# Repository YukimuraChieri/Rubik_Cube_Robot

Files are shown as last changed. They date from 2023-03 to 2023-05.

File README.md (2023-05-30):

# Rubik_Cube_Robot
## 毕业设计：双臂二指魔方机器人  
该项目完成于2022年6月  
整体结构图如下：  
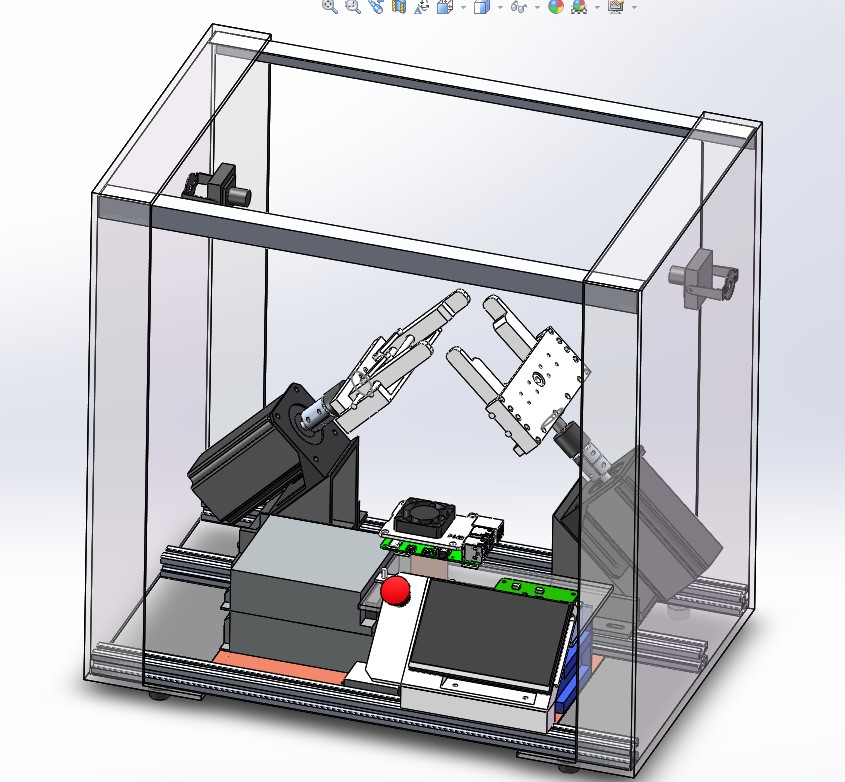
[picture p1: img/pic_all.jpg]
  
该机器人使用两个闭环步进电机驱动夹爪旋转，使用高速舵机驱动夹爪动作。  
机器人的控制系统主要为下位机+上位机，下位机与上位机之间通过USB串口通信  
下位机硬件基于STM32F103C8T6制作，上位机硬件为树莓派4B，操作系统为Ubuntu+ROS。  
其中上位机外接了一个触摸屏用于显示人机交互界面，该界面采用Qt开发。
仓库中的catkin_ws为ROS部分的代码。  
Robot_HMI为Qt界面的代码。  
matlab程序为计算S曲线加减速的相关代码。  

## 注意事项  
STM32下位机程序的开发环境为keil5，如果出现乱码的情况需要将编码设置为GB2312。  
PCB工程需要使用Altium Designer09软件打开。  
整体结构需要使用solidworks2015或者以上版本的软件打开。  
  
更多细节见《毕业论文_最终版1》

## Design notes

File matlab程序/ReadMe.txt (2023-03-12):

test_1.m 为步进电机S曲线加减速曲线绘制程序
test_2.m 步进电机S曲线加减速脉冲周期序列生成程序

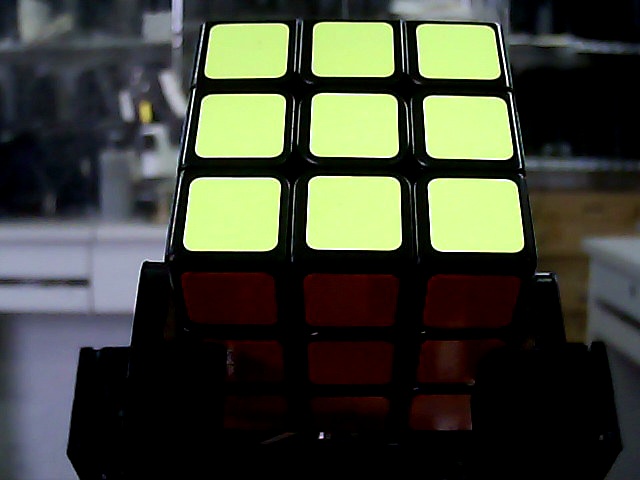
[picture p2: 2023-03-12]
catkin_ws/src/face_read/img/right_face12185.jpg

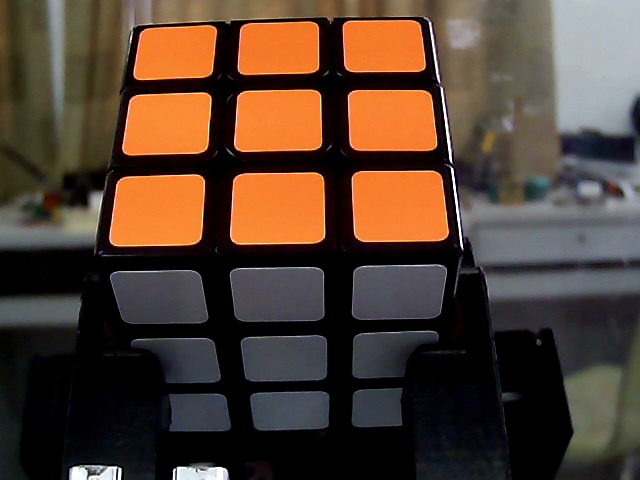
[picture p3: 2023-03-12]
catkin_ws/src/face_read/img/left_face12185.jpg

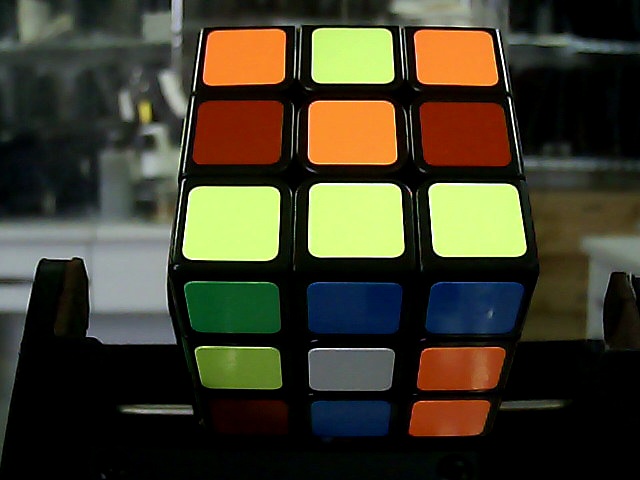
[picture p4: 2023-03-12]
catkin_ws/src/face_read/img/right_face7710.jpg

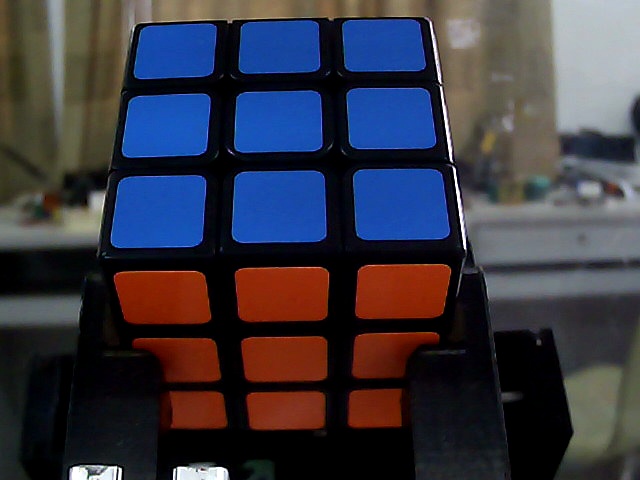
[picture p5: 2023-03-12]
catkin_ws/src/face_read/img/left_face12473.jpg

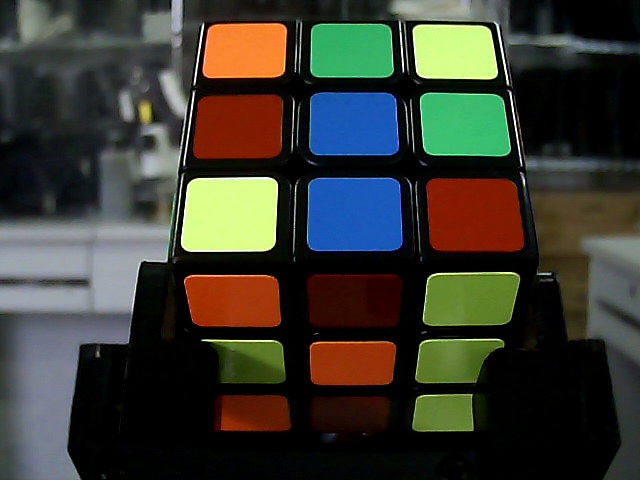
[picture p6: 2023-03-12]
catkin_ws/src/face_read/img/right_face8291.jpg

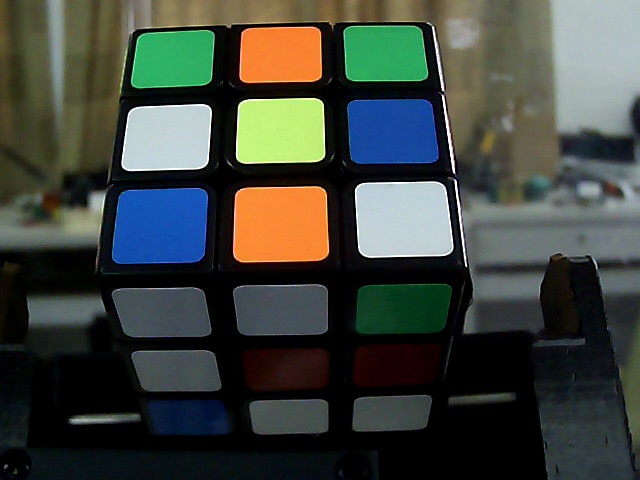
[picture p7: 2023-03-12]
catkin_ws/src/face_read/img/left_face7710.jpg

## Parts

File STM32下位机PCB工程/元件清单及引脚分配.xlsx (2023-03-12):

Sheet: Sheet1
STM32控制板元件清单
序号 | 名称 | 封装 | 数量 | 单价 | 备注
1 | STM32F103C8T6 | LQF-48 | 1 | 5 | MCU
2 | TLP521-1 | SOP-4 | 2 | 0.35 | 光耦隔离器件
3 | AMS1117-3.3 | SOT-223 | 1 |  | 3.3V LDO稳压芯片
4 | S8550 | SOT-23R | 6 |  | PNP三极管
5 | 8M贴片晶振 | SMD-5032 | 1
6 | A型6.3V10uf 106E钽电容 | 0805 | 2 | 0.41
7 | 104贴片电容 | 0805 | 9 | 0.02
8 | 20pF贴片电容 | 0805 | 2
9 | 贴片LED | 0805 | 2
10 | 22R贴片电阻 | 0805 | 2
11 | 330R贴片电阻 | 0805 | 2
12 | 1K贴片电阻 | 0805 | 6
13 | 4.7K贴片电阻 | 0805 | 6
14 | 10K贴片电阻 | 0805 | 3
15 | mini usb母座 | USB/SM0.8-6H5 | 1 | 0.11 | Mini USB接口
16 | 3P接线端子 | KF301-3P | 2 |  | 电机接口
17 | 4P接线端子 | KF301-4P | 1 |  | 电源接口
18 | 3P直排针 | HDR1X3 | 2 |  | 舵机接口
19 | 4P直排针 | HDR1X4 | 2 |  | SWD、串口接口
20 | XH2.54MM插座 | HDR1X2 | 1 |  | 紧急开关接口
21 | PCB |  | 1 |  | 需要在PCB生产厂家打样

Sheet: Sheet2
STM32控制板元件清单
序号 | 名称 | 封装 | 数量 | 备注
1 | STM32F103C8T6 | LQF-48 | 1 | MCU
2 | TLP521-1 | SOP-4 | 2 | 光耦隔离器件
3 | AMS1117-3.3 | SOT-223 | 1 | 3.3V LDO稳压芯片
4 | S8550 | SOT-23R | 6 | PNP三极管
5 | 8M贴片晶振 | SMD-5032 | 1
6 | A型6.3V10uf 106E钽电容 | 0805 | 2
7 | 104贴片电容 | 0805 | 9
8 | 20pF贴片电容 | 0805 | 2
9 | 贴片LED | 0805 | 2
10 | 22R贴片电阻 | 0805 | 2
11 | 330R贴片电阻 | 0805 | 2
12 | 1K贴片电阻 | 0805 | 6
13 | 4.7K贴片电阻 | 0805 | 6
14 | 10K贴片电阻 | 0805 | 3
15 | mini usb母座 | USB/SM0.8-6H5 | 1 | Mini USB接口
16 | 3P接线端子 | KF301-3P | 2 | 电机接口
17 | 4P接线端子 | KF301-4P | 1 | 电源接口
18 | 3P直排针 | HDR1X3 | 2 | 舵机接口
19 | 4P直排针 | HDR1X4 | 2 | SWD、串口接口
20 | XH2.54MM插座 | HDR1X2 | 1 | 紧急开关接口

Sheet: IO分配表
IO端口分配表
引脚 | 功能 |  | 备注
PB13 | PUL1 | 电机1 | TIM1_CH1N
PA4 | DIR1
PA5 | ENA1
PB14 | PUL2 | 电机2 | TIM1_CH2N
PA7 | DIR2
PB0 | ENA2
PB6 | PWM1 | 舵机1 | TIM4_CH1
PB7 | PWM2 | 舵机2 | TIM4_CH2
PA9 | TXD1 | 串口1
PA10 | RXD1
PA11 | D- | USB接口
PA12 | D+
PA13 | SWDIO | SWD接口
PA14 | SWCLK
PB12 |  | 紧急开关 | TIM1_BKIN
PC13 | LED1 | LED指示灯

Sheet: 通信协议格式
通信协议格式
执行指令 | AT
应答 | OK
参数说明
舵机操作指令
执行指令 | AT+SERVO=<LR>,<CMD>
应答 | AT+SERVO OK
参数说明 | <LR> | LEFT:左舵机 | RIGHT:右舵机 | ALL:所有舵机
 | <CMD> | CLAMP:夹紧 | LOOSE:松开
步进电机操作指令
执行指令 | AT+STEP=<LR>,<DIR>,<ANG>
应答 | AT+STEP OK
参数说明 | <LR> | LEFT:左电机 | RIGHT:右电机 | ALL:所有电机
 | <DIR> | ‘+’：顺时针旋转 | ‘-’：逆时针旋转
 | <ANG> | 90：90度 | 180：180度
应答 | Error
说明 | 指令格式错误
应答 | Alarm
说明 | 急停开关按下
 |  | AT+SERVO=RIGHT,LOOSE
 |  | AT+STEP=RIGHT,+,180

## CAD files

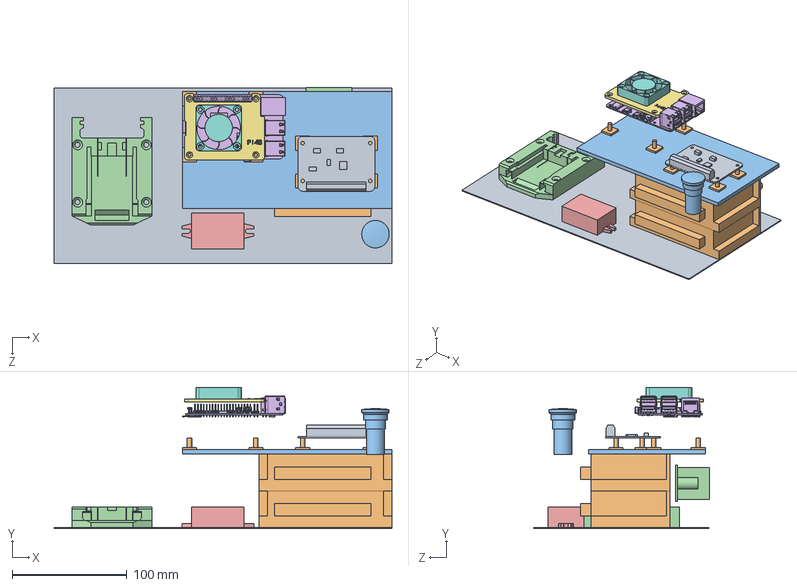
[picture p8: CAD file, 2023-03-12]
魔方机器人整体结构/电控部分/装配体_电池.SLDASM
295.0 x 123.3 x 153.5 mm
底板
电机驱动器 x 2
亚克力板
DC12V转7.5V稳压模块
DC12V转5V稳压模块
Raspberry Pi 41
风扇支架
风扇4010
STM32控制板
塑料座 x 8
急停开关
电池卡座_V3

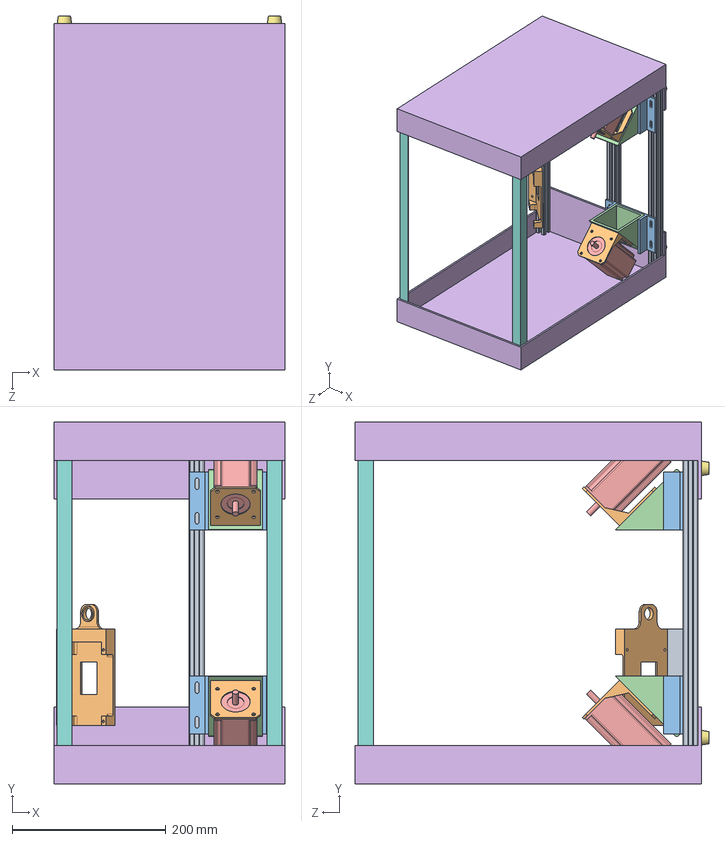
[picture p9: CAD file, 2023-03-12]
魔方机器人整体结构/底座/底座_装配体.SLDASM
300.0 x 470.0 x 460.0 mm
2020铝型材_350 x 3
电机支架 x 2
电机座1 x 2
电机座2 x 2
57步进电机 x 2
亚克力支架 x 2
脚垫20-17-10 x 4
L铝型材_460 x 2
触摸屏底座
屏幕支架

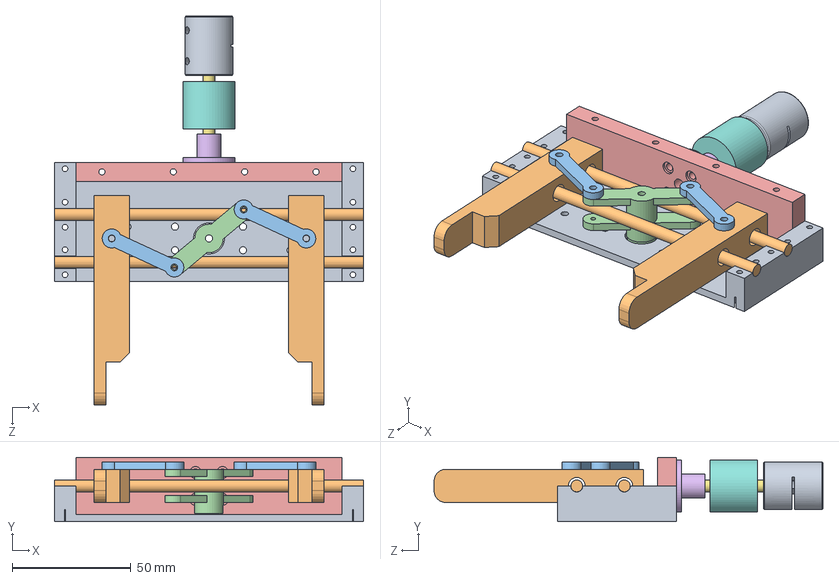
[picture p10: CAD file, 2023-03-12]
魔方机器人整体结构/魔方平行夹/装配体1.SLDASM
130.0 x 27.0 x 163.5 mm
底座
滑轴 x 2
连杆2 x 2
主轴连杆
后卡位片_更改
法兰联轴器
M5光轴_50
导电滑环
联轴器
滑块2 x 2

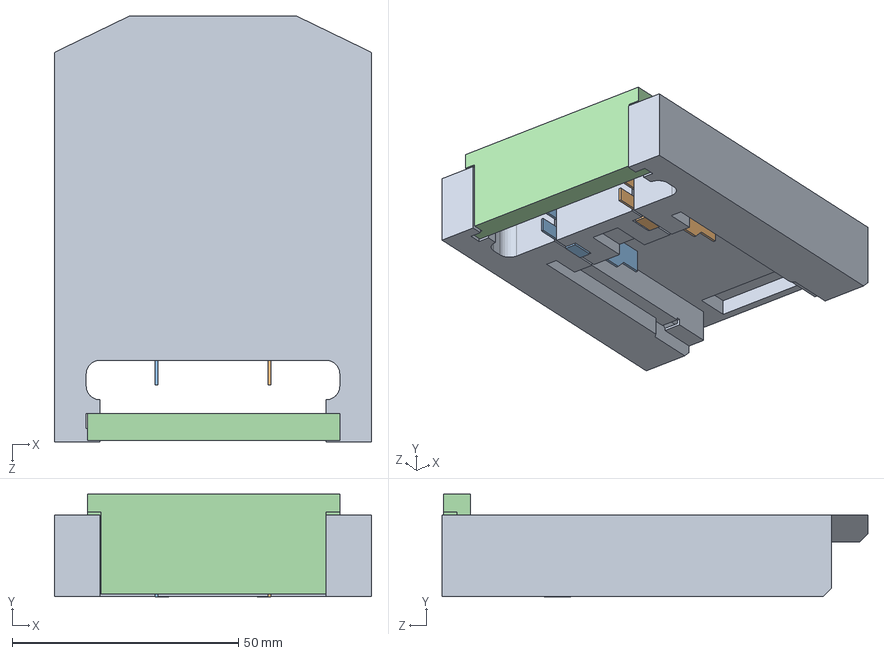
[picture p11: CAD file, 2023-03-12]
魔方机器人整体结构/电池卡座/电池座.SLDASM
70.0 x 22.7 x 94.0 mm
电池卡座
电极片左
电极片右
盖板

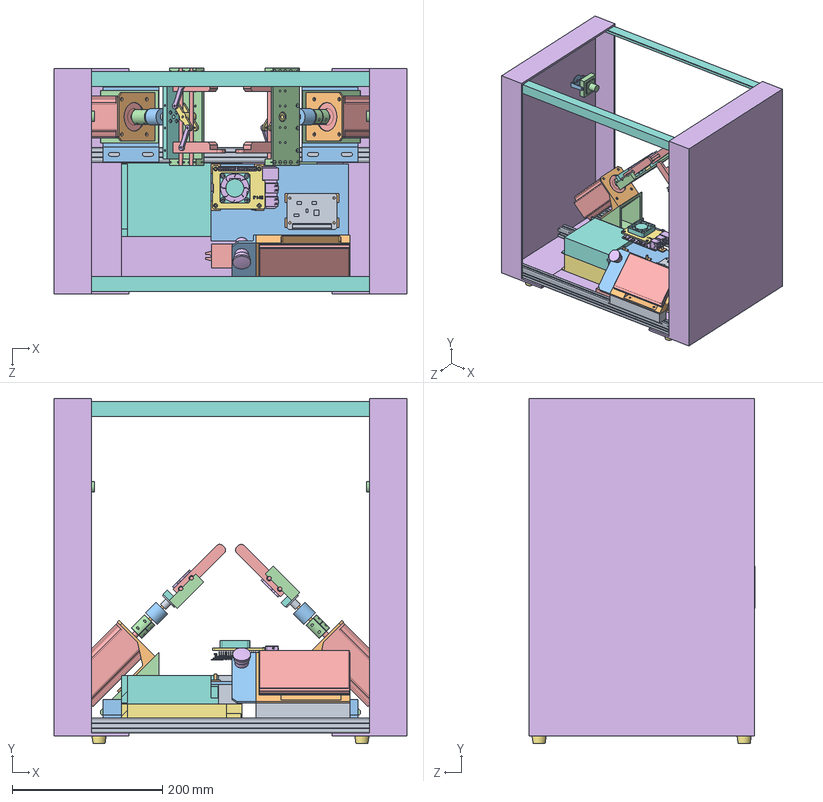
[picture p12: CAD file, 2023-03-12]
魔方机器人整体结构/总装配体.SLDASM
470.0 x 460.0 x 300.9 mm
2020铝型材_350 x 3
电机支架 x 2
电机座1 x 2
电机座2 x 2
57步进电机 x 2
亚克力支架 x 2
脚垫20-17-10 x 4
L铝型材_460 x 2
触摸屏底座
屏幕支架
屏幕侧板
底座 x 2
滑轴 x 4
连杆2 x 4
主轴连杆 x 2
后卡位片_更改 x 2
法兰联轴器 x 2
M5光轴_50 x 2
导电滑环 x 2
联轴器 x 2
滑块2 x 4
底板
12V开关电源
28V开关电源
侧板
电机驱动器 x 2
亚克力板
DC12V转7.5V稳压模块
DC12V转5V稳压模块
Raspberry Pi 41
风扇支架
风扇4010
STM32控制板
塑料座 x 8
摄像头支架 x 2
摄像头 x 2
触摸屏
急停开关

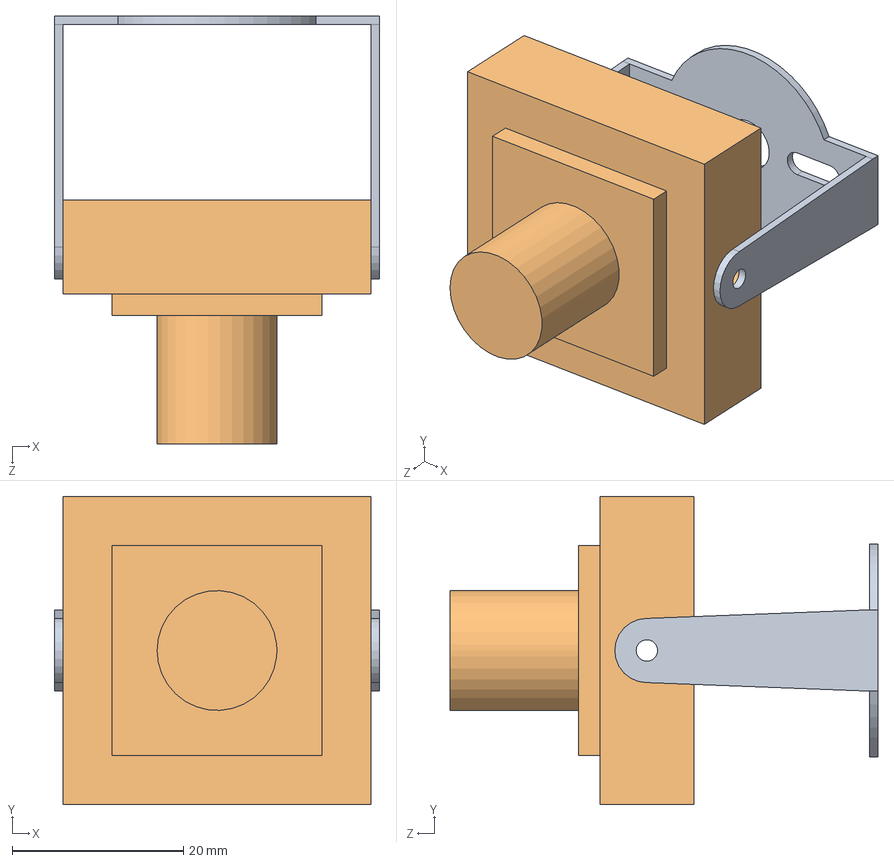
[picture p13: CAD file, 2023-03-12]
魔方机器人整体结构/电控部分/USB摄像头.SLDASM
38.0 x 36.0 x 50.0 mm
摄像头支架
摄像头

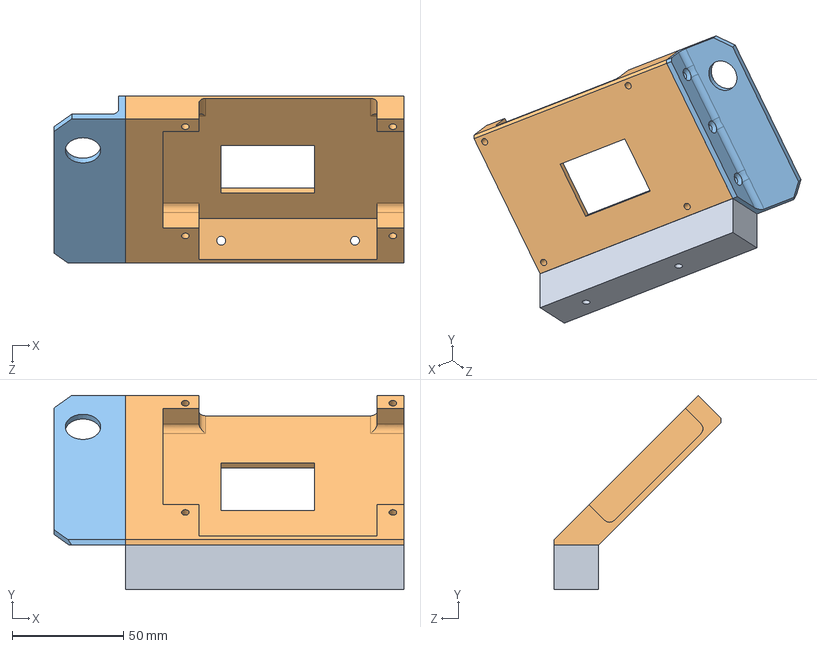
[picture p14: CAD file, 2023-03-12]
魔方机器人整体结构/底座/触摸屏支架.SLDASM
157.0 x 87.2 x 75.0 mm
触摸屏底座
屏幕支架
屏幕侧板

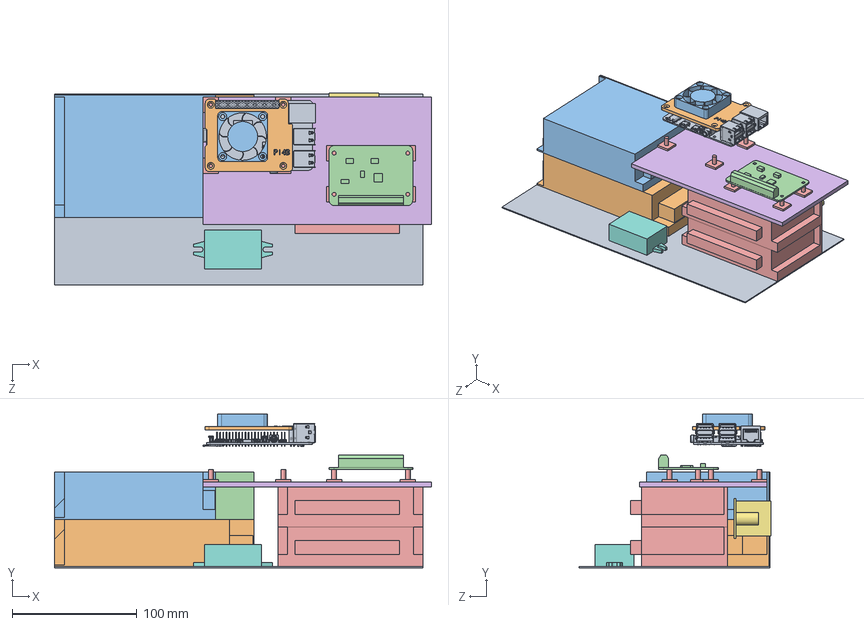
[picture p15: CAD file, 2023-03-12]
魔方机器人整体结构/电控部分/装配体2.SLDASM
302.0 x 123.3 x 153.5 mm
底板
12V开关电源
28V开关电源
侧板
电机驱动器 x 2
亚克力板
DC12V转7.5V稳压模块
DC12V转5V稳压模块
Raspberry Pi 41
风扇支架
风扇4010
STM32控制板
塑料座 x 8

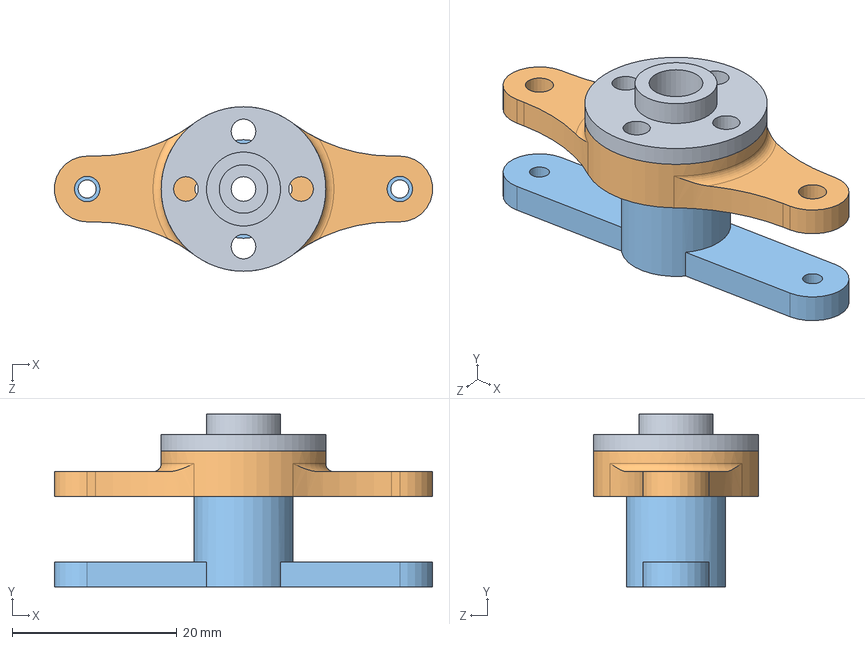
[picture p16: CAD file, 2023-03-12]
魔方机器人整体结构/魔方平行夹/主轴连杆_装配体.SLDASM
45.9 x 21.0 x 20.0 mm
舵机舵盘
主轴连杆下_2022_4_21
主轴连杆上2

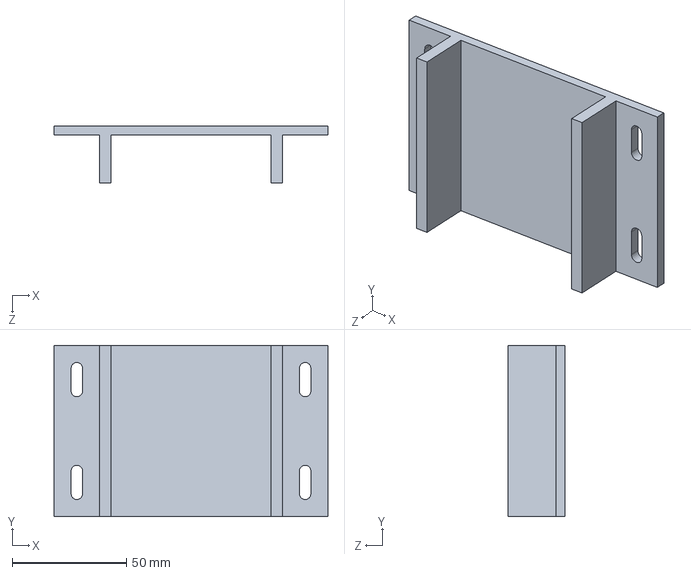
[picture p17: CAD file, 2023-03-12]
魔方机器人整体结构/底座/电机座1.SLDPRT
120.0 x 75.0 x 25.0 mm

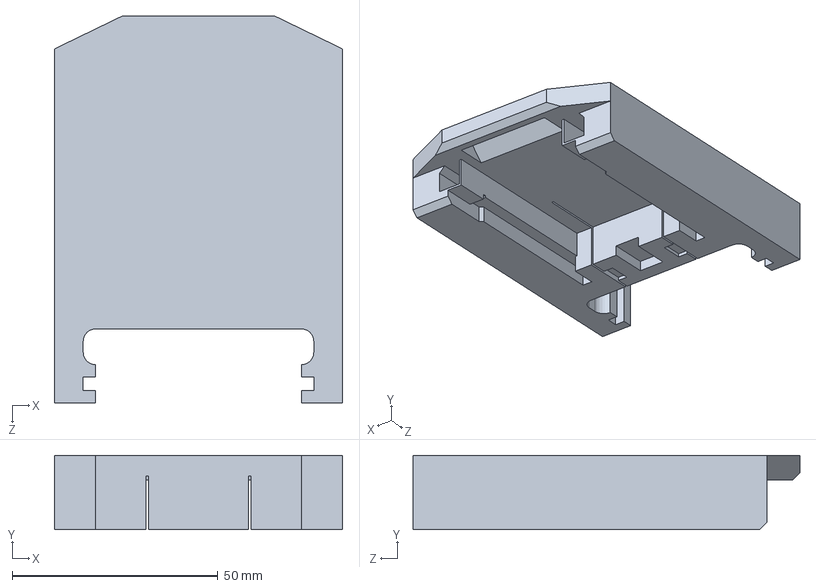
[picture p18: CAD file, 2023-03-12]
魔方机器人整体结构/电池卡座/电池卡座.SLDPRT
70.0 x 18.0 x 94.0 mm

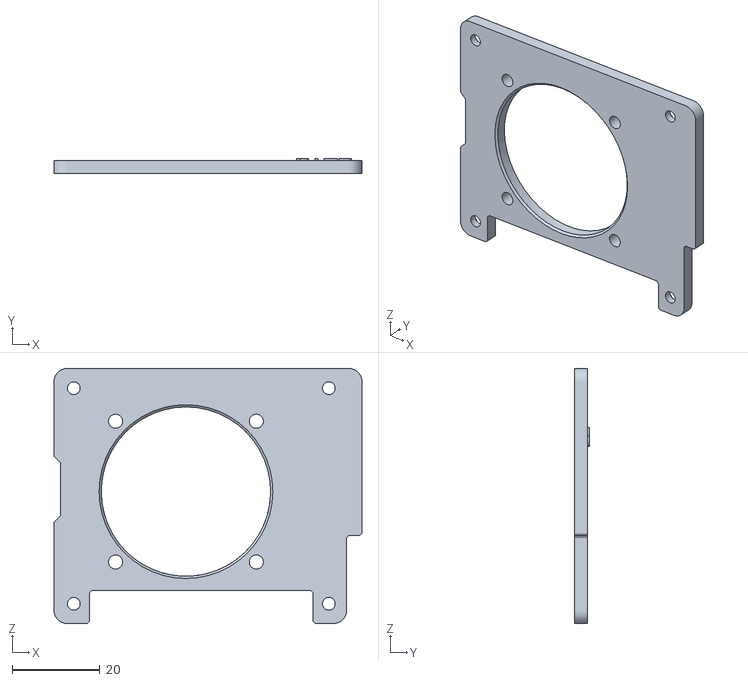
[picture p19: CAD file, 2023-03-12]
魔方机器人整体结构/风扇支架.STL
70.0 x 3.45 x 58.0

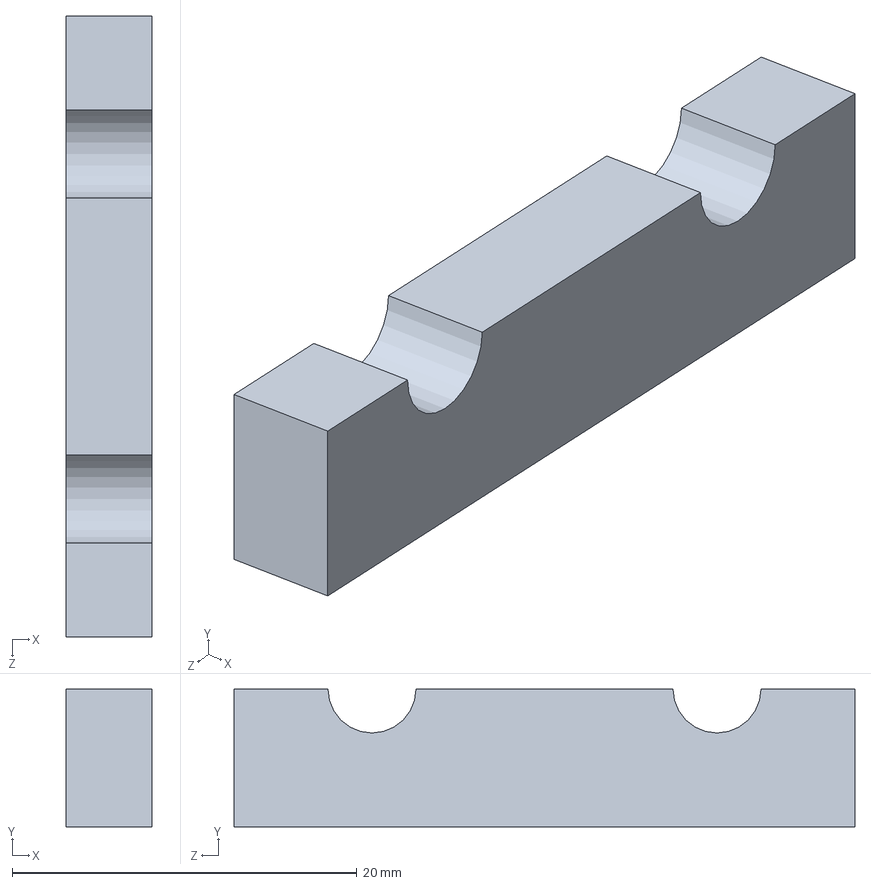
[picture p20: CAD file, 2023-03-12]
魔方机器人整体结构/魔方平行夹/夹块.SLDPRT
5.00 x 8.00 x 36.0 mm

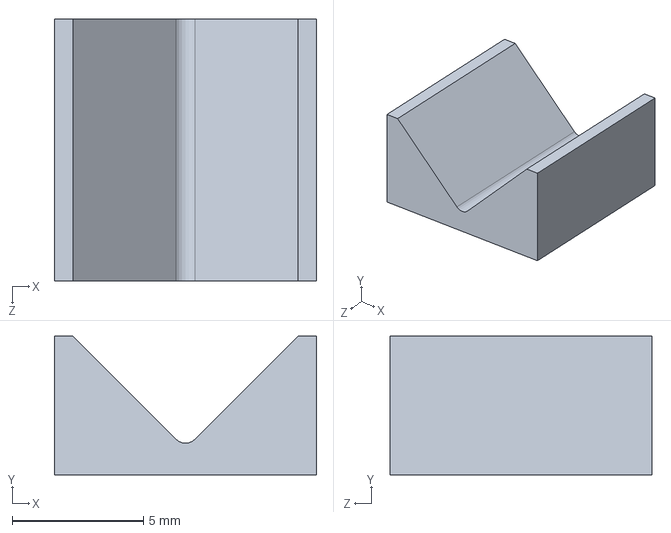
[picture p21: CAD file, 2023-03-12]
魔方机器人整体结构/灯条固定座1.SLDPRT
10.0 x 5.29 x 10.0 mm

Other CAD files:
魔方机器人整体结构/电控部分/塑料座.SLDPRT
魔方机器人整体结构/电池卡座/电极片.SLDPRT
魔方机器人整体结构/魔方平行夹/主轴连杆下2.SLDPRT
魔方机器人整体结构/屏幕侧板.STL
魔方机器人整体结构/主轴连杆下.SLDPRT
魔方机器人整体结构/主轴连杆下.STL
魔方机器人整体结构/主轴连杆下_2022_5_2.STL
魔方机器人整体结构/屏幕支架.STL
魔方机器人整体结构/底座/2020铝型材.SLDPRT
魔方机器人整体结构/底座/2020铝型材_150.SLDPRT
魔方机器人整体结构/底座/2020铝型材_350.SLDPRT
魔方机器人整体结构/底座/2020铝型材_80.SLDPRT
魔方机器人整体结构/底座/57步进电机.SLDPRT
魔方机器人整体结构/底座/L铝型材_460.SLDPRT
魔方机器人整体结构/底座/M5光轴_50.SLDPRT
魔方机器人整体结构/底座/亚克力支架.SLDPRT
魔方机器人整体结构/底座/亚克力板_加工.DWG
魔方机器人整体结构/底座/亚克力板_加工.SLDDRW
魔方机器人整体结构/底座/亚克力板_加工.SLDPRT
魔方机器人整体结构/底座/导电滑环.SLDPRT
魔方机器人整体结构/底座/屏幕侧板.SLDPRT
魔方机器人整体结构/底座/屏幕支架.SLDPRT
魔方机器人整体结构/底座/底板.SLDPRT
魔方机器人整体结构/底座/电机座2.SLDPRT
魔方机器人整体结构/底座/电机支架.SLDPRT
魔方机器人整体结构/底座/联轴器.SLDPRT
魔方机器人整体结构/底座/脚垫20-17-10.sldprt
魔方机器人整体结构/底座/触摸屏底座.SLDPRT
魔方机器人整体结构/滑环垫片.SLDPRT
魔方机器人整体结构/灯条固定座1.STL
魔方机器人整体结构/灯条封头.SLDPRT
魔方机器人整体结构/灯条封头.STL
魔方机器人整体结构/电控部分/12V开关电源.SLDPRT
魔方机器人整体结构/电控部分/28V开关电源.SLDPRT
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

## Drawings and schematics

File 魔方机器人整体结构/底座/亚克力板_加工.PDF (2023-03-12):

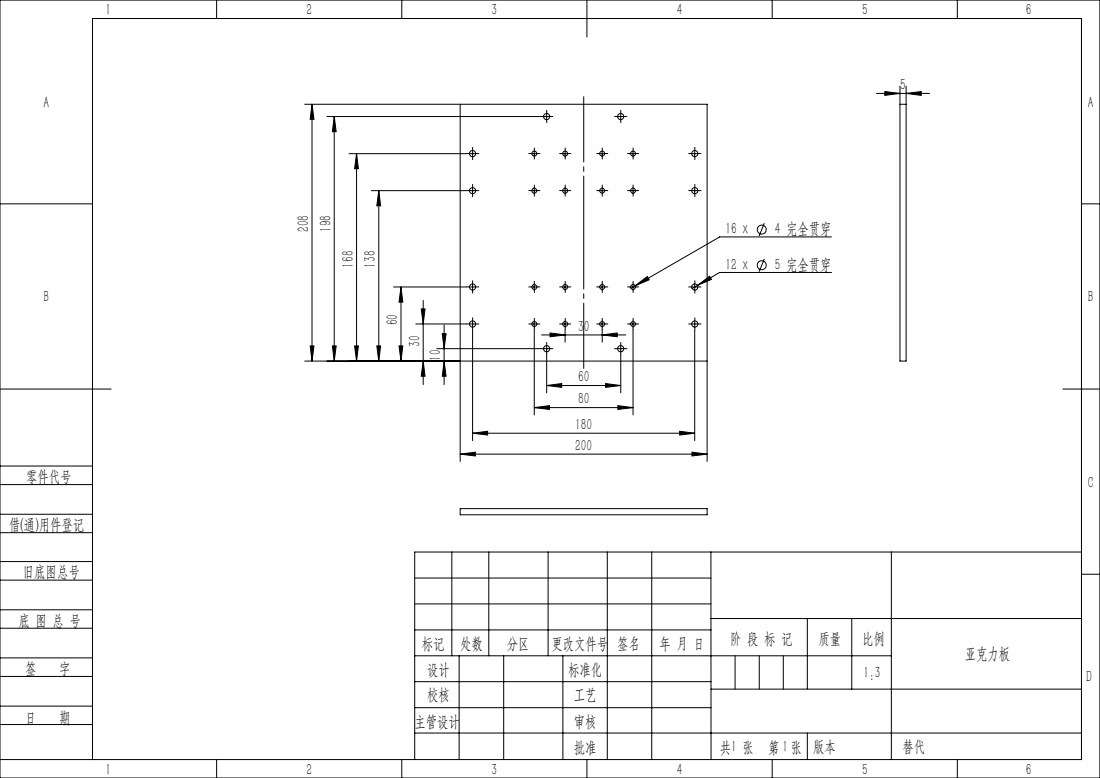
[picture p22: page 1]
5 完全贯穿; 4 完全贯穿

阶 段 标 记 | 质量 | 比例 | 亚克力板

标记 | 处数 | 分区 | 更改文件号 | 签名 | 年 月 日

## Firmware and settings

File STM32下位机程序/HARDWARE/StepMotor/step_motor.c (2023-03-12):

#include "step_motor.h"

// 旋转列表指针
u16* S_Curve_List;
u16 len;						// 长度
u8 motor_AB = '\0';	// 左右电机选择
u8 stepRun = 0;			// 电机运行状态
u8 brkFlag = 0;			// 刹车信号
u16 PulCnt = 0;			// 脉冲计数
u8 stepFinish = 0;	// 电机完成状态


// S曲线低速旋转90度脉冲周期列表，最大加速度20r/s^2，加减速时间0.1S
const u16 Rot90_LS_List[250] = {
	9999,	9523,	8398,	7194,	6185,	5396,	4783,	4300,	3911,	3594,	
	3329,	3105,	2914,	2747,	2602,	2473,	2359,	2256,	2164,	2080,	
	2003,	1933,	1868,	1809,	1754,	1702,	1655,	1611,	1571,	1535,	
	1502,	1471,	1442,	1416,	1391,	1368,	1347,	1327,	1308,	1290,	
	1273,	1257,	1241,	1227,	1213,	1200,	1188,	1176,	1164,	1154,	
	1143,	1133,	1124,	1115,	1106,	1098,	1090,	1082,	1075,	1067,	
	1061,	1054,	1048,	1041,	1035,	1030,	1024,	1019,	1014,	1009,	
	1004,	1000,	995,	991,	987,	983,	979,	975,	972,	968,	
	965,	962,	959,	956,	953,	950,	948,	945,	943,	940,	
	938,	936,	934,	932,	930,	928,	926,	925,	923,	922,	
	920,	919,	918,	917,	916,	915,	914,	913,	912,	911,	
	911,	910,	910,	909,	909,	909,	908,	908,	908,
	908,	908,	908,	908,	908,	908,	908,	908,	908,	908,	
	908,	908,	908,	908,	909,	909,	909,	910,	910,	911,	
	911,	912,	913,	914,	915,	916,	917,	918,	919,	920,	
	922,	923,	925,	926,	928,	930,	932,	934,	936,	938,	
	940,	943,	945,	948,	950,	953,	956,	959,	962,	965,	
	968,	972,	975,	979,	983,	987,	991,	995,	1000,	1004,	
	1009,	1014,	1019,	1024,	1030,	1035,	1041,	1048,	1054,	1061,	
	1067,	1075,	1082,	1090,	1098,	1106,	1115,	1124,	1133,	1143,	
	1154,	1164,	1176,	1188,	1200,	1213,	1227,	1241,	1257,	1273,	
	1290,	1308,	1327,	1347,	1368,	1391,	1416,	1442,	1471,	1502,	
	1535,	1571,	1611,	1655,	1702,	1754,	1809,	1868,	1933,	2003,	
	2080,	2164,	2256,	2359,	2473,	2602,	2747,	2914,	3105,	3329,	
	3594,	3911,	4300,	4783,	5396,	6185,	7194,	8398,	9523,	9999, 1
};

// S曲线低速旋转180度脉冲周期列表，最大加速度20r/s^2，加减速时间0.2S
const u16 Rot180_LS_List[501] = {
	9999,	9090,	7328,	5888,	4892,	4194,	3684,	3297,	2993,	2747,	
	2544,	2374,	2228,	2102,	1993,	1896,	1809,	1732,	1662,	1599,	
	1541,	1488,	1439,	1394,	1352,	1313,	1277,	1243,	1212,	1182,	
	1154,	1127,	1102,	1078,	1056,	1035,	1014,	995,	976,	959,	
	942,	925,	910,	895,	881,	868,	855,	843,	832,	821,	
	811,	801,	792,	783,	774,	766,	758,	750,	743,	736,	
	729,	723,	716,	710,	704,	699,	693,	688,	682,	677,	
	672,	668,	663,	659,	654,	650,	646,	642,	638,	634,	
	631,	627,	624,	620,	617,	614,	610,	607,	604,	601,	
	599,	596,	593,	590,	588,	585,	583,	580,	578,	575,	
	573,	571,	569,	567,	564,	562,	560,	558,	556,	555,	
	553,	551,	549,	547,	546,	544,	542,	541,	539,	537,	
	536,	534,	533,	532,	530,	529,	527,	526,	525,	523,	
	522,	521,	520,	519,	517,	516,	515,	514,	513,	512,	
	511,	510,	509,	508,	507,	506,	505,	504,	503,	502,	
	502,	501,	500,	499,	498,	498,	497,	496,	495,	495,	
	494,	493,	493,	492,	491,	491,	490,	489,	489,	488,	
	488,	487,	487,	486,	486,	485,	485,	484,	484,	483,	
	483,	483,	482,	482,	481,	481,	481,	480,	480,	480,	
	479,	479,	479,	479,	478,	478,	478,	478,	477,	477,	
	477,	477,	477,	476,	476,	476,	476,	476,	476,	476,	
	476,	475,	475,	475,	475,	475,	475,	475,	475,	475,	
	475,	475,	475,	475,	475,	475,	475,	475,	475,	475,	
	475,	475,	475,	475,	475,	475,	475,	475,	475,	475,	
	475,	475,	475,	475,	475,	475,	475,	475,	475,	475,	
	475,	475,	475,	475,	475,	475,	475,	475,	475,	475,	
	475,	475,	475,	475,	475,	475,	475,	475,	475,	475,	
	475,	475,	475,	475,	475,	475,	475,	475,	475,	475,	
	475,	475,	475,	475,	475,	475,	475,	475,	475,	476,	
	476,	476,	476,	476,	476,	476,	476,	477,	477,	477,	
	477,	477,	478,	478,	478,	478,	479,	479,	479,	479,	
	480,	480,	480,	481,	481,	481,	482,	482,	483,	483,	
	483,	484,	484,	485,	485,	486,	486,	487,	487,	488,	
	488,	489,	489,	490,	491,	491,	492,	493,	493,	494,	
	495,	495,	496,	497,	498,	498,	499,	500,	501,	502,	
	502,	503,	504,	505,	506,	507,	508,	509,	510,	511,	
	512,	513,	514,	515,	516,	517,	519,	520,	521,	522,	
	523,	525,	526,	527,	529,	530,	532,	533,	534,	536,	
	537,	539,	541,	542,	544,	546,	547,	549,	551,	553,	
	555,	556,	558,	560,	562,	564,	567,	569,	571,	573,	
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
};


// S曲线中速旋转90度脉冲周期列表，最大加速度40r/s^2，加减速时间0.1S
const u16 Rot90_MS_List[250] = {
	9999,	7142,	4596,	3459,	2824,	2414,	2124,	1907,	1737,	1600,	
	1487,	1392,	1311,	1240,	1178,	1123,	1074,	1030,	991,	954,	
	921,	891,	864,	840,	818,	798,	780,	763,	748,	733,	
	720,	708,	696,	685,	675,	666,	657,	648,	640,	633,	
	626,	619,	612,	606,	600,	594,	589,	584,	579,	574,	
	570,	565,	561,	557,	554,	550,	546,	543,	540,	537,	
	534,	531,	528,	525,	523,	520,	518,	516,	513,	511,	
	509,	507,	505,	504,	502,	500,	499,	497,	496,	494,	
	493,	492,	490,	489,	488,	487,	486,	485,	484,	483,	
	482,	482,	481,	480,	480,	479,	478,	478,	477,	477,	
	477,	476,	476,	476,	476,	475,	475,	475,	475,	
	475,	475,	475,	475,	475,	475,	475,	475,	475,	475,		
	475,	475,	475,	475,	475,	475,	475,	475,	475,	475,	
	475,	475,	475,	475,	475,	475,	475,	475,	475,	475,	
	475,	475,	475,	475,	475,	476,	476,	476,	476,	477,	
	477,	477,	478,	478,	479,	480,	480,	481,	482,	482,	
	483,	484,	485,	486,	487,	488,	489,	490,	492,	493,	
	494,	496,	497,	499,	500,	502,	504,	505,	507,	509,	
	511,	513,	516,	518,	520,	523,	525,	528,	531,	534,	
	537,	540,	543,	546,	550,	554,	557,	561,	565,	570,	
	574,	579,	584,	589,	594,	600,	606,	612,	619,	626,	
	633,	640,	648,	657,	666,	675,	685,	696,	708,	720,	
	733,	748,	763,	780,	798,	818,	840,	864,	891,	921,	
	954,	991,	1030,	1074,	1123,	1178,	1240,	1311,	1392,	1487,	
	1600,	1737,	1907,	2124,	2414,	2824,	3459,	4596,	7142,	9999,	 1
};
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

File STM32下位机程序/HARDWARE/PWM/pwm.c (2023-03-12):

#include "pwm.h"

u8 servoRun = 0;		// 舵机运行状态
u8 leftAngle = 0;		// 左舵机当前角度
u8 rightAngle = 0;	// 右舵机当前角度
u8 setLeft = 0;			// 左舵机设定角度
u8 setRight = 0;		// 右舵机设定角度
u8 servoFinish = 0;	// 舵机完成状态
u8 servo_speed = 4;	// 舵机夹紧速度

void TIM4_PWM_Init(u16 arr,u16 psc)
{
	//此部分需手动修改IO口设置
	RCC->APB1ENR|=1<<2; 		//TIM4时钟使能    
	RCC->APB2ENR|=1<<3;    	//使能PORTB时钟 	 
	GPIOB->CRL&=0X00FFFFFF;	//PB6/7输出
	GPIOB->CRL|=0XBB000000;	//复用功能输出

	TIM4->ARR=arr;			//设定计数器自动重装值 
	TIM4->PSC=psc;			//预分频器分频数
//	TIM4->DIER|=1<<0;		//允许更新中断
	
	TIM4->CCMR1|=7<<4;  	//CH1 PWM2模式		 
	TIM4->CCMR1|=1<<3; 		//CH1 预装载使能
	TIM4->CCER|=1<<1;   	//OC1 输出反相
	TIM4->CCER|=1<<0;			//OC1 输出使能	 

	TIM4->CCMR1|=7<<12;		//CH2 PWM2模式		 
	TIM4->CCMR1|=1<<11;		//CH2 预装载使能	   
	TIM4->CCER|=1<<5;   	//OC2 输出反相
	TIM4->CCER|=1<<4;			//OC2 输出使能
	
	TIM4->CR1=0x0080;   //ARPE使能 
	TIM4->CR1|=0x01;    //使能定时器4
	
	CH1_PWM_VAL = Angle_to_PWM(0);	//初始化右舵机PWM占空比
	CH2_PWM_VAL = Angle_to_PWM(0);	//初始化左舵机PWM占空比
	
	MY_NVIC_Init(1,2,TIM4_IRQn,2);		//抢占1，子优先级2，组2
}

//角度值转换为PWM比较值（适用于180度舵机 ）
u16 Angle_to_PWM(u16 angle)
{
	angle = angle * 4 + 180;
	
	return 7200 - angle;
}


//设置舵机角度函数
void Set_Angle(u8 angle, char dir)
{
	switch(dir)
	{
		case 'A':	setLeft = angle;	break;
		case 'B':	setRight = angle;	break;
	}
	
	if(setLeft != leftAngle || setRight != rightAngle)
	{
		TIM4->DIER |= 1<<0;	// 允许更新中断
		servoRun = 1;				// 舵机运行状态置1
	}
	else
		servoFinish = 1;				// 舵机完成状态置1
}


// 获取舵机的运行状态
u8 Get_Servo_Status(void)
{
	return servoRun;		// 返回舵机运行状态
}


// 获取舵机的完成状态
u8 Get_Servo_Finish(void)
{
	u8 temp = servoFinish;
	
	servoFinish = 0;
	
	return temp;		// 返回舵机完成状态
}


// 设置舵机速度
void Set_Servo_Speed(u8 speed)
{
	servo_speed = speed;
}


// 定时器4中断服务函数
void TIM4_IRQHandler(void)
{
	if(TIM4->SR&0X0001)	//溢出中断
	{
		if(leftAngle < setLeft)	// 左舵机小于设定角度
		{
			leftAngle += (setLeft - leftAngle)/servo_speed + 1;
			CH2_PWM_VAL = Angle_to_PWM(leftAngle);
		}
		else if(leftAngle > setLeft)	// 左舵机大于设定角度
		{
			leftAngle -= (leftAngle - setLeft)/servo_speed + 1;
			CH2_PWM_VAL = Angle_to_PWM(leftAngle);
		}
		
		if(rightAngle < setRight)	// 右舵机小于设定角度
		{
			rightAngle += (setRight - rightAngle)/servo_speed + 1;
			CH1_PWM_VAL = Angle_to_PWM(rightAngle);
		}
		else if(rightAngle > setRight)	// 右舵机大于设定角度
		{
			rightAngle -= (rightAngle - setRight)/servo_speed + 1;
			CH1_PWM_VAL = Angle_to_PWM(rightAngle);
		}
		
		if(leftAngle == setLeft && rightAngle == setRight)	// 如果左右舵机均达到设定角度
		{
			servoRun = 0;						// 舵机运行状态置0
			servoFinish = 1;				// 舵机完成状态置1
			TIM4->DIER &= ~(1<<0);	// 关闭中断
		}
		
		TIM4->SR&=~(1<<0);	//清除中断标志位
	}
}

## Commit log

2023-03-12 项目提交
    [12V开关电源.SLDPRT, 2020铝型材.SLDPRT, 2020铝型材_150.SLDPRT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]
2023-03-12 添加毕业论文
2023-05-30 更新Qt界面与代码
